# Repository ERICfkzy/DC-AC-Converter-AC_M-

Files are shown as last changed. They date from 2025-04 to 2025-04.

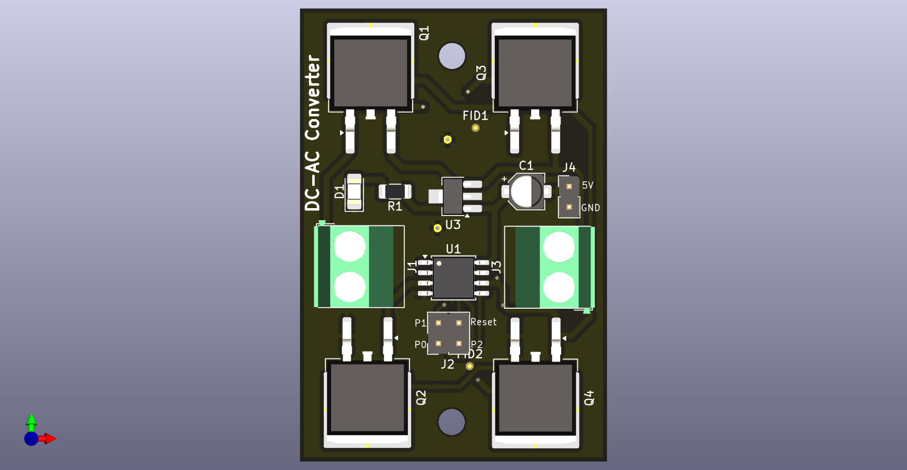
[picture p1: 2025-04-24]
Render/AC_M V2-3.png

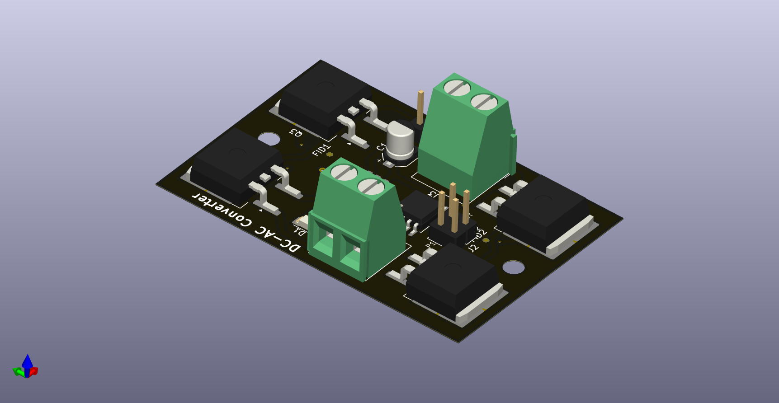
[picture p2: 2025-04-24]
Render/AC_M V2-5.png

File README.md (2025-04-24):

**DC-AC Converter PCB:**
Power supply unit for the simple transformer model
It converts the DC voltage (9v) to AC voltage at 50Hz to drive the transformer's primary. 
It is stepped up at the secondary based on the turns ratio of the transformer.
ATtiny85 chip generates PWM signals to switch ON/OFF the MOSFETs (2 N-channel).
Switching of the MOSFETs creates square waveform, hence converting DC to AC signals.
Same schematic diagram with two variants of PCB i.e. SMD-version1 and PTH-version2.

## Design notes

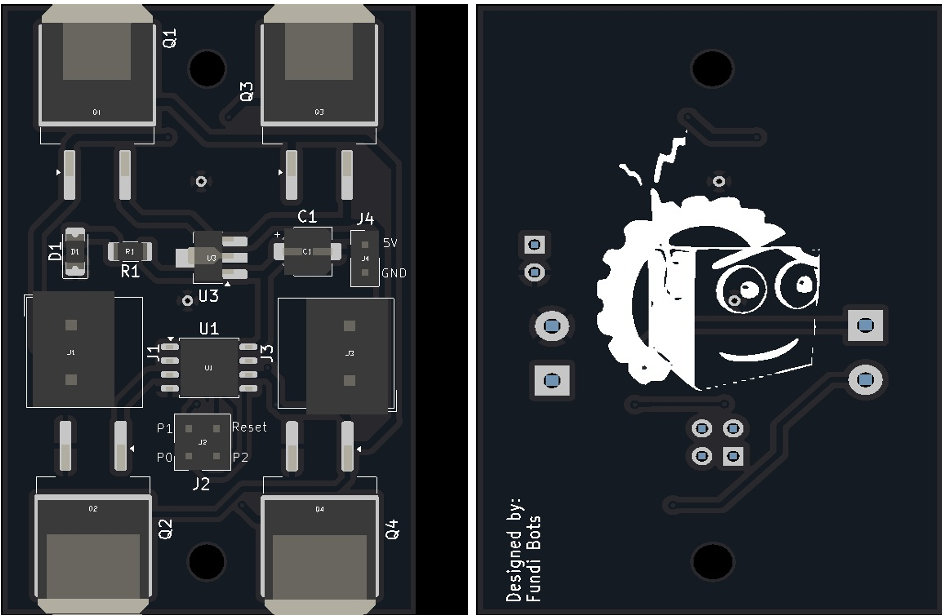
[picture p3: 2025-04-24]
Render/AC_M V2-7.png

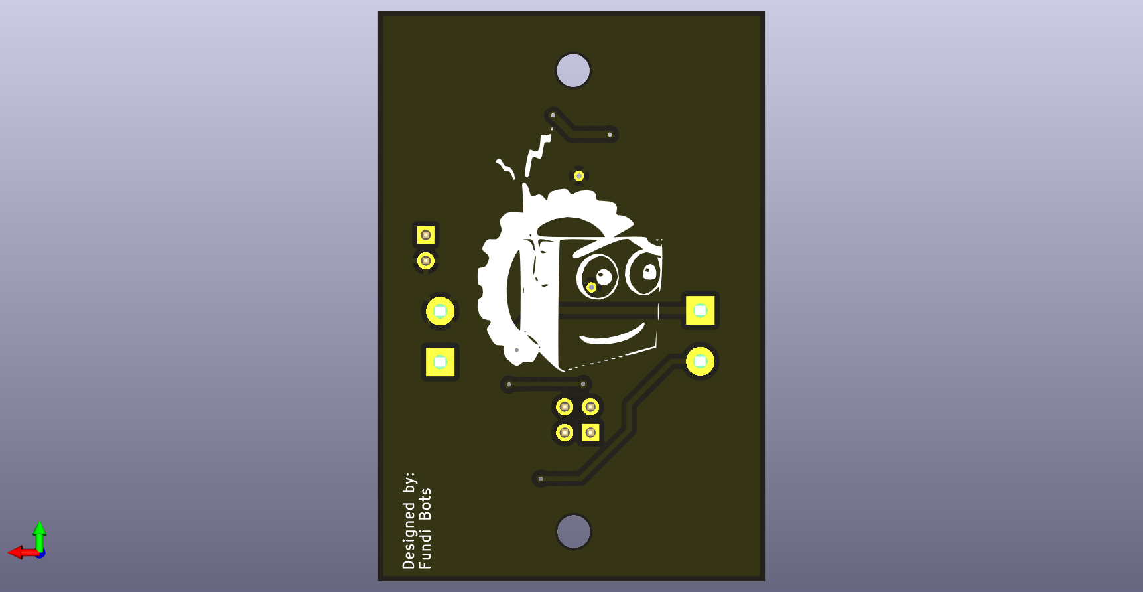
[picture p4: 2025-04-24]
Render/AC_M V2-4.png

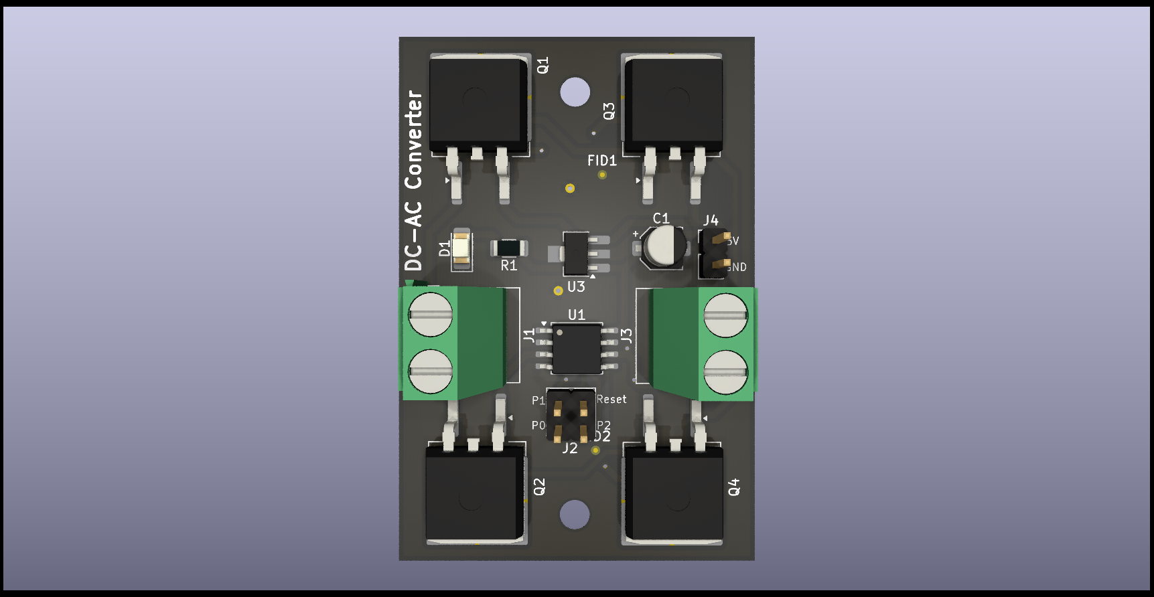
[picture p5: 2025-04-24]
Render/AC_M V2-1.png

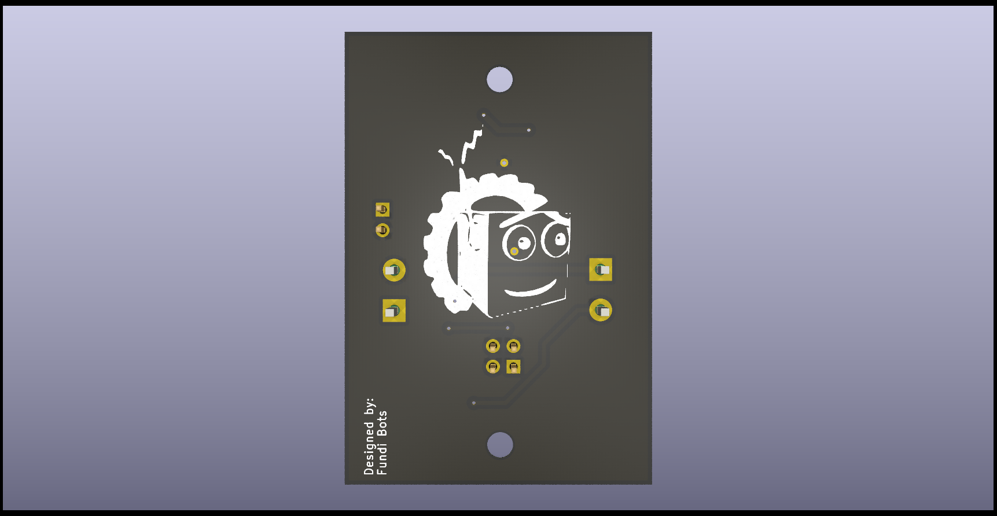
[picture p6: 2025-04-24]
Render/AC_M V2-2.png

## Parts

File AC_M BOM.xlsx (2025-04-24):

Designator | Footprint | Quantity | Value
C1 | CP_Elec_4x5.3 | 1 | C_Polarized_Small_US
D1 | 1206 | 1 | LED
J1, J3 | TerminalBlock_MetzConnect_Type011_RT05502HBWC_1x02_P5.00mm_Horizontal | 2 | Screw_Terminal_3.5mm_2
J2 | PinHeader_2x02_P2.54mm_Vertical | 1 | Conn_02x02_Counter_Clockwise
J4 | PinHeader_1x02_P2.54mm_Vertical | 1 | Conn_01x02
Q1, Q3 | TO-263-2 | 2 | IRF9540N
Q2, Q4 | TO-263-2 | 2 | IRFZ44NSTRLPBF
R1 | 1206 | 1 | R
U1 | SOP-8_5.28x5.23mm_P1.27mm | 1 | ATtiny85V-10P
U3 | SOT-89-3_Handsoldering | 1 | L78L05_SOT89

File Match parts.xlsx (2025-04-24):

Designator | Footprint | Quantity | Value | Recommended Component | Recommended Manufacturer | Link | Description | Matching | Goods ID
C1 | CP_Elec_4x5.3 | 1 | C_Polarized_Small_US | UWT1H010MCL1GB | Nichicon |  | SMD Aluminum Electrolytic Capacitor SMD,D4xL5.4mm 1µF ±20% 50V 1000Hrs@105? | Pass
D1 | 1206 | 1 | LED | TJ-S3216B11YJY-A3 | TOGIALED |  | LED blue LED 1206 460 ~470nm 80~200mcd Front Mounting | Pass
J1, J3 | TerminalBlock_MetzConnect_Type011_RT05502HBWC_1x02_P5.00mm_Horizontal | 2 | Screw_Terminal_3.5mm_2 | WJ301V-5.0-2P | Kangnex |  | Screw type terminal 2Pin spacing: 5mm, 1 row straight plug blue | Pass
J2 | PinHeader_2x02_P2.54mm_Vertical | 1 | Conn_02x02_Counter_Clockwise | B-2100S04P-B110 | ckmtw |  | The spacing between rows of pins is 2.54mm, and the straight insertion is gold-plated 4pin (2X2) | Pass
J4 | PinHeader_1x02_P2.54mm_Vertical | 1 | Conn_01x02 | A2541WV-2P | CJT |  | Pin Headers spacing 2.54mm 2Pins (1x2) brass gold-plated straight plug | Pass
Q1, Q3 | TO-263-2 | 2 | IRF9540N | IRF9540NSTRRPBF | Infineon |  | MOSFETs P-channel VDS=100V ID=23A VGS=±20V D2PAK | Pass
Q2, Q4 | TO-263-2 | 2 | IRFZ44NSTRLPBF | IRFZ44NSTRLPBF | Infineon |  | 55V 49A 3.8W 17.5mO@10V,25A 4V@250uA N Channel D2PAK MOSFETs ROHS | Pass
R1 | 1206 | 1 | R | RC1206FR-07330RL | Yageo |  | Chip Resistors 1206 330O ±1% 1/4W ±100ppm/? | Pass
U1 | SOP-8_5.28x5.23mm_P1.27mm | 1 | ATtiny85V-10P | ATTINY85-20SU | Microchip |  | 8-bit Microcontrollers - MCU AVR 8K FLSH 512B EE 512B SRAM ADC 5V | Pass
U3 | SOT-89-3_Handsoldering | 1 | L78L05_SOT89 | PJ73AL33SQ | PJ |  | Linear Voltage Regulators / LDOs Positive Vin=20V Vout=3.3V 300mA | Pass

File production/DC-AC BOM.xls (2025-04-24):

Designator* | Quantity* | Manufacturer Part Number* | Manufacturer | Package/Footprint | Description
C1 | 1 | RVT0J470M0405 |  | SMD,D4xL5.4mm | SMD Aluminum Electrolytic Capacitor SMD,D4xL5.4mm 47µF ±20% 6.3V 2000Hrs@105℃
D1 | 1 | TJ-S3216B11YJY-A3 |  | 1206 | LED blue LED 1206 460 ~470nm 80~200mcd Front Mounting
Q1,Q3 | 2 | IRF9540NSTRLPBF |  | TO-263-2(D²PAK) | 100V 23A 3.1W 117mΩ@10V,14A 4V@250uA P Channel D2PAK MOSFETs ROHS
Q2,Q4 | 2 | IRFZ44NSTRLPBF |  | TO-263-2(D²PAK) | 55V 49A 3.8W 17.5mΩ@10V,25A 4V@250uA N Channel D2PAK MOSFETs ROHS
R1 | 1 | RTT063300FTP |  | 1206 | Chip Resistors 1206 330Ω ±1% 1/4W ±100ppm/℃
U1 | 1 | ATTINY85-20SU |  | SOP-8 5.28x5.23mm_P1.27mm(SOIC8_208MIL) | 8-bit Microcontrollers - MCU AVR 8K FLSH 512B EE 512B SRAM ADC 5V
U3 | 1 | 78L05 |  | SOT89-3 | Linear Voltage Regulators / LDOs Vin=30V Vout=5V 100mA 80dB@(120Hz)

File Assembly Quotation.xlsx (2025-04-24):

生产数量: | 175 | 贴片元件种类: | 7 | 插件元件种类: | 3
贴片面数: | 单面 | 贴片元件数量: | 9 | 插件元件数量: | 4
焊接插件: | 是 | 贴片焊盘数量: | 29 | 插件焊盘数量: | 10
空贴物料: | 0 | 孔上焊盘数: |  | 线材物料: | 0
总计: |  | 板子大小: | 5.60X3.80cm | 上锡面积:
规格参数 | 封装 | 位号 | 单机用量 | 型号 | 生成总用量 | 是否有元件库 | 焊盘数 | 总焊盘数 | 装配类型 | 确认状态
L78L05_SOT89 | SOT-89-3_Handsoldering | U3 | 1 |  | 175 | Yes | 3 | 3 | SMT | Confirmed
IRFZ44NSTRLPBF | TO-263-2 | Q2,Q4 | 2 |  | 350 | Yes | 3 | 6 | SMT | Confirmed
ATtiny85V-10P | SOP-8_5.28x5.23mm_P1.27mm | U1 | 1 |  | 175 | Yes | 8 | 8 | SMT | Confirmed
R | 1206 | R1 | 1 |  | 175 | Yes | 2 | 2 | SMT | Confirmed
IRF9540N | TO-263-2 | Q1,Q3 | 2 |  | 350 | Yes | 3 | 6 | SMT | Confirmed
C_Polarized_Small_US | CP_Elec_4x5.3 | C1 | 1 |  | 175 | Yes | 2 | 2 | SMT | Confirmed
Conn_01x02 | PinHeader_1x02_P2.54mm_Vertical | J4 | 1 |  | 175 | Yes | 2 | 2 | THT | Confirmed
LED | 1206 | D1 | 1 |  | 175 | Yes | 2 | 2 | SMT | Confirmed
Conn_02x02_Counter_Clockwise | PinHeader_2x02_P2.54mm_Vertical | J2 | 1 |  | 175 | Yes | 4 | 4 | THT | Confirmed
Screw_Terminal_3.5mm_2 | TerminalBlock_MetzConnect_Type011_RT05502HBWC_1x02_P5.00mm_Horizontal | J1,J3 | 2 |  | 350 | Yes | 2 | 4 | THT | Confirmed

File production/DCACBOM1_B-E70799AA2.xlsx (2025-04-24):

BOM File: |  | DCACBOM1 |  |  |  |  |  |  | Order ID： | B-E70799AA2 |  |  |  | Quote Time: | 2025/03/25 15:20:59
Purchase Quantity： |  | 175 pcs |  |  |  |  |  |  | BOM Total ($)： | 846.48
Inquiry |  |  |  |  |  |  |  |  | HQNextPCB-Quotation
S/N | Designator* | Quantity* | Manufacturer Part Number* | Manufacturer | Package /Footprint | Description | Procurement Type | Customer Note | Quote MPN | Quote Brand | Package /Footprint | Plan Qty | Overage Amount | Quote Qty | Unit Price($) | Subtotal($) | Lead Time | Question from HQ NextPCB | Customer Reply
1 | C1 | 1 | RVT0J470M0405 |  | SMD,D4xL5.4mm | SMD Aluminum Electrolytic Capacitor SMD,D4xL5.4mm 47µF ±20% 6.3V 2000Hrs@105℃ |  |  | RVT0J470M0405 | HONOR | SMD,D4xL5.4mm | 175 | 15 | 190 | 0.01913 | 3.63 | In Stock
2 | D1 | 1 | TJ-S3216B11YJY-A3 |  | 1206 | LED blue LED 1206 460 ~470nm 80~200mcd Front Mounting |  |  | TJ-S3216B11YJY-A3 | TOGIALED | 1206 | 175 | 10 | 185 | 0.02569 | 4.75 | In Stock
6 | Q1,Q3 | 2 | IRF9540NSTRLPBF |  | TO-263-2(D²PAK) | 100V 23A 3.1W 117mΩ@10V,14A 4V@250uA P Channel D2PAK MOSFETs ROHS |  |  | IRF9540NSTRLPBF | TECH PUBLIC(台舟) | D²PAK | 350 | 3 | 353 | 0.33512 | 118.3 | 4-7 WD
7 | Q2,Q4 | 2 | IRFZ44NSTRLPBF |  | TO-263-2(D²PAK) | 55V 49A 3.8W 17.5mΩ@10V,25A 4V@250uA N Channel D2PAK MOSFETs ROHS |  |  | IRFZ44NSTRLPBF | Infineon | D²PAK | 350 | 2 | 352 | 0.50394 | 177.39 | 4-7 WD
8 | R1 | 1 | RTT063300FTP |  | 1206 | Chip Resistors 1206 330Ω ±1% 1/4W ±100ppm/℃ |  |  | RTT063300FTP | RALEC | 1206 | 175 | 10 | 185 | 0.00248 | 0.46 | In Stock
9 | U1 | 1 | ATTINY85-20SU |  | SOP-8 5.28x5.23mm_P1.27mm(SOIC8_208MIL) | 8-bit Microcontrollers - MCU AVR 8K FLSH 512B EE 512B SRAM ADC 5V |  |  | ATTINY85-20SU | Microchip | SOIC8_208MIL | 175 | 0 | 180 | 1.57782 | 284.01 | In Stock
10 | U3 | 1 | 78L05 |  | SOT89-3 | Linear Voltage Regulators / LDOs Vin=30V Vout=5V 100mA 80dB@(120Hz) |  |  | 78L05 | CBI | SOT-23 | 175 | 15 | 190 | 0.01815 | 3.45 | In Stock
 |  |  |  |  |  |  |  |  |  |  |  |  |  |  |  | 591.99

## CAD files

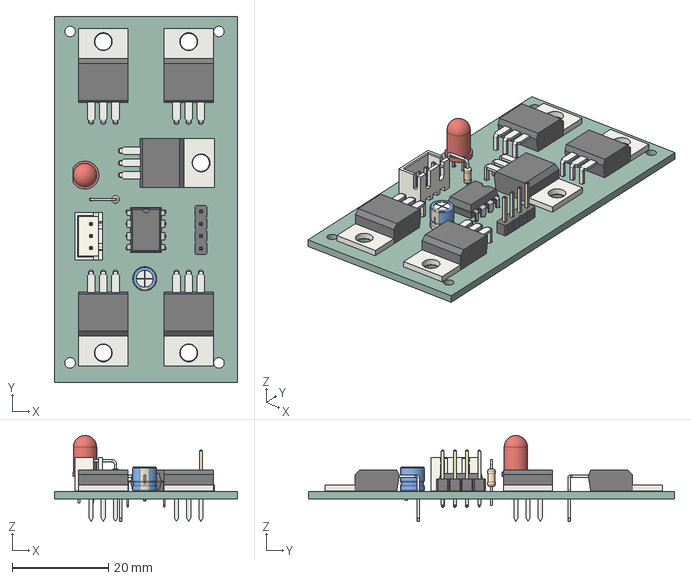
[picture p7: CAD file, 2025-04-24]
AC_M V2.step
38.1 x 76.2 x 17.9 mm
_autosave-AC_M PCB

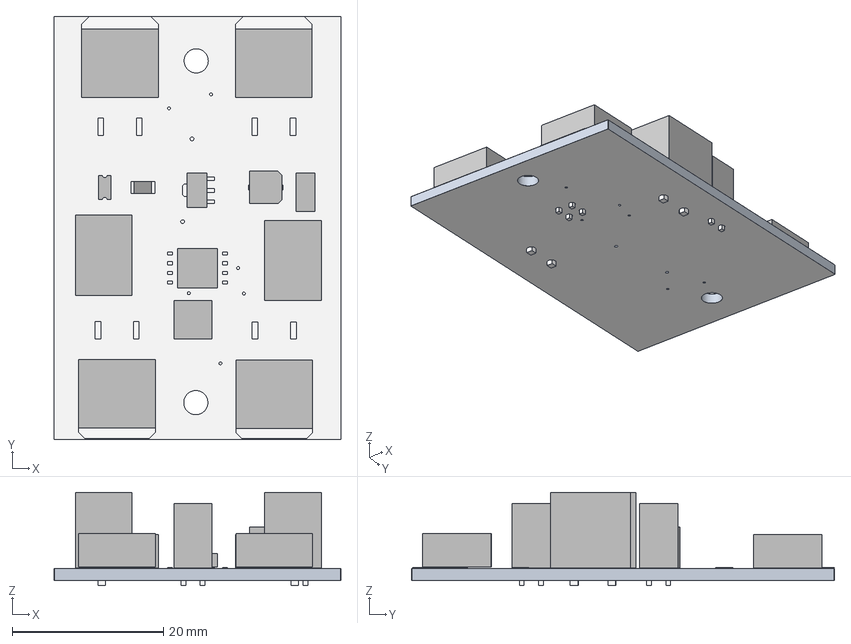
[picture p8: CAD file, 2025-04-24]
Render/AC_M V2.step
38.0 x 56.0 x 12.3 mm

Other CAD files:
AC_M V2 3D.step

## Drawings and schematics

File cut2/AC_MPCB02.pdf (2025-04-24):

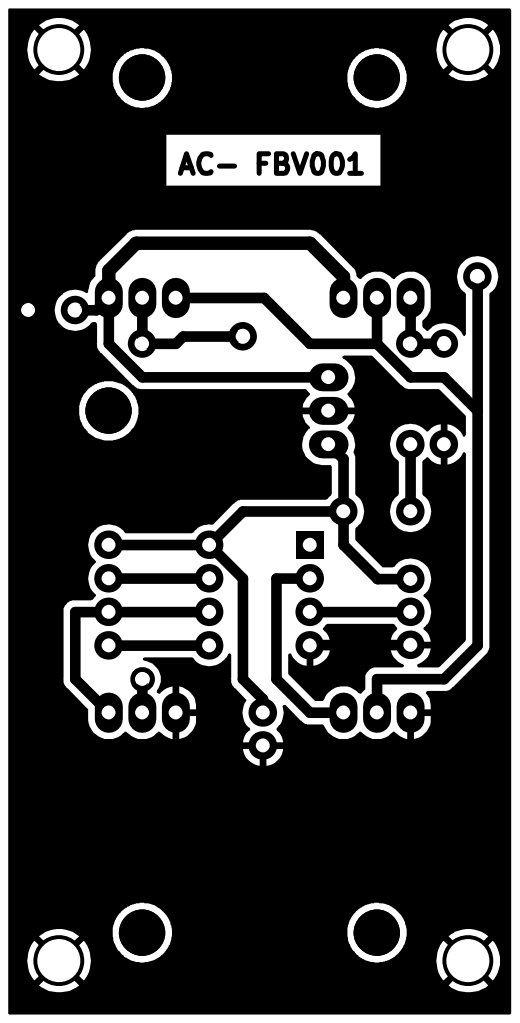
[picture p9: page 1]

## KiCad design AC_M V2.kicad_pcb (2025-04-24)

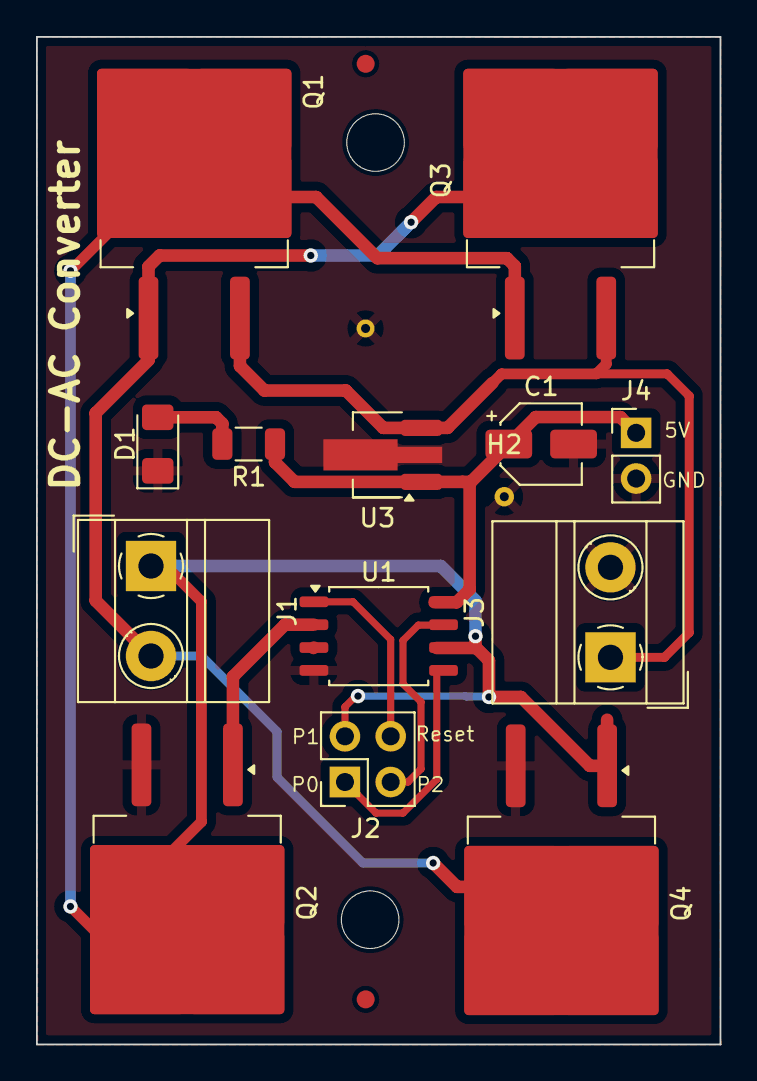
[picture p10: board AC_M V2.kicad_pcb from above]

Board: 2 copper layers, 38.0 x 56.0 mm, 19 parts (0 on the bottom side), 10 nets.

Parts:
C1: C_Polarized_Small_US; CP_Elec_4x5.3
D1: LED; LED_1206_3216Metric_Pad1.42x1.75mm_HandSolder
FID1, FID2: Fiducial; Fiducial_0.5mm_Mask1mm
H1, H2: MountingHole_Pad; MountingHole_2.2mm_M2_DIN965_Pad
H3, H4: MountingHole; MountingHole_3.2mm_M3
J1, J3: Screw_Terminal_3.5mm_2; TerminalBlock_MetzConnect_Type011_RT05502HBWC_1x02_P5.00mm_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
J2: Conn_02x02_Counter_Clockwise; PinHeader_2x02_P2.54mm_Vertical
J4: Conn_01x02; PinHeader_1x02_P2.54mm_Vertical
Q1, Q3: IRF9540N; TO-263-2
Q2, Q4: IRFZ44NSTRLPBF; TO-263-2
R1: R; R_1206_3216Metric
U1: ATtiny85V-10P; SOP-8_5.28x5.23mm_P1.27mm
U3: L78L05_SOT89; SOT-89-3_Handsoldering

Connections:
/Reset: J2.4, U1.1 (~RESET/PB5)
/pin0: J2.1, U1.5 (AREF/PB0)
/pin2: J2.3, U1.7 (PB2)
GND: C1.2, D1.1 (K), H1.1, H2.1, J3.2, J4.2, Q2.3, Q4.3, U1.4 (GND), U3.2 (GND)
unnamed: D1.2 (A), R1.2
unnamed: J1.1, J2.2, Q1.2 (D), Q2.2, Q3.1 (G), Q4.1, U1.6 (PB1)
unnamed: J1.2, Q1.1 (G), Q3.2 (D), Q4.2
unnamed: J3.1, Q1.3 (S), Q3.3 (S), U3.3 (IN)
unnamed: C1.1, J4.1, R1.1, U1.8 (VCC), U3.1 (OUT)
unnamed: Q2.1, U1.2 (XTAL1/PB3)
